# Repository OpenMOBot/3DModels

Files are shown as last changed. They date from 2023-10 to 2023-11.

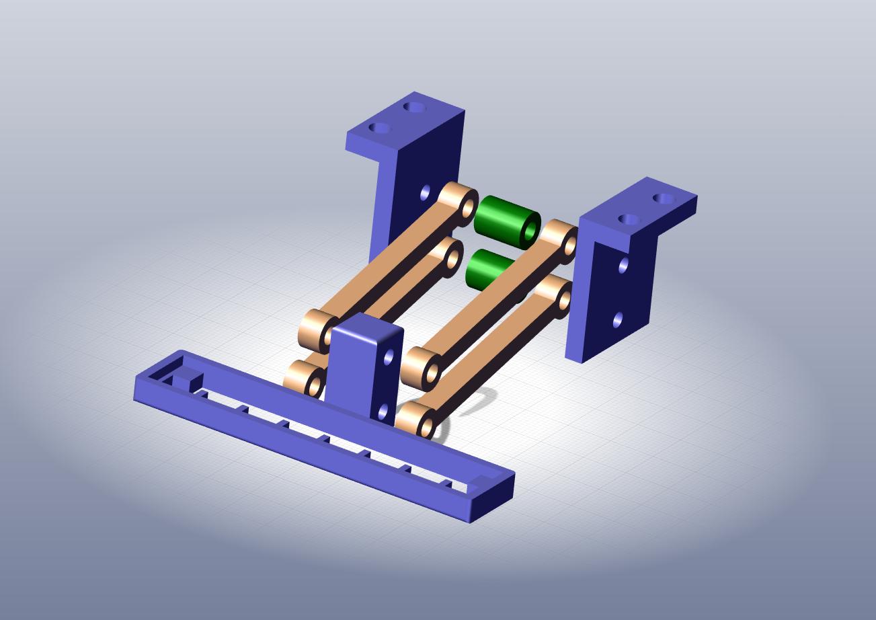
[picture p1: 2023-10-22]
images/sensor_holder_parts_assembly.jpg

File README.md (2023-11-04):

#  <span style="color: #32FAE5"> 1. How to assemble the 3D printed chassis :rocket:</span> 

## <span style="color: #32FAE5">1.1 Needed parts to be printed</span> 

- 1 :heavy_multiplication_x: [chassis](https://github.com/OpenMOBot/3DModels/blob/17b4ab84576b85b1f8e65cfbf05c9b37ba42eddf/design_stl/chassis/chassis.STL) <br />
- 4 :heavy_multiplication_x: [motor mount](https://github.com/OpenMOBot/3DModels/blob/17b4ab84576b85b1f8e65cfbf05c9b37ba42eddf/design_stl/chassis/motor_mount.STL) <br />
- 2 :heavy_multiplication_x: [encoder wheel](https://github.com/OpenMOBot/3DModels/blob/17b4ab84576b85b1f8e65cfbf05c9b37ba42eddf/design_stl/encoder_wheels/encoder_wheel_v4_20.STL) <br />
- 2 :heavy_multiplication_x: [mounting part](https://github.com/OpenMOBot/3DModels/blob/17b4ab84576b85b1f8e65cfbf05c9b37ba42eddf/design_stl/sensor_holder/mounting_part.STL) <br />
- 1 :heavy_multiplication_x: [sensor holder](https://github.com/OpenMOBot/3DModels/blob/17b4ab84576b85b1f8e65cfbf05c9b37ba42eddf/design_stl/sensor_holder/sensor_holder.STL) <br /> 
- 2 :heavy_multiplication_x: [spacer](https://github.com/OpenMOBot/3DModels/blob/17b4ab84576b85b1f8e65cfbf05c9b37ba42eddf/design_stl/sensor_holder/spacer.STL) <br />
- 4 :heavy_multiplication_x: [sturt](https://github.com/OpenMOBot/3DModels/blob/17b4ab84576b85b1f8e65cfbf05c9b37ba42eddf/design_stl/sensor_holder/sturt.STL) <br />
- 1  :heavy_multiplication_x:  [ultrasonic_holder](https://github.com/OpenMOBot/3DModels/blob/main/design_stl/chassis/ultrasonic-holder.stl)

## <span style="color: #32FAE5">1.2 Assemble the QTR-8RC sensor holder</span>

- Needed parts
sensor_holder_parts

- Assemble the mentioned parts
sensor_holder_parts_assembly

- Secure the sensor holder by using M3x30 and M3x25 bolts along with M3 nuts.
<p align="center">
    
</p>

## <span style="color: #32FAE5">1.3 Mount the caster wheel to the chassis</span>
- use four M4x8 bolts along with four M4 nuts and washers.
<p align="center">
    
</p>

## <span style="color: #32FAE5">1.4 Mount the Arduino and the DC motor driver L298N</span>

### Materials:
- Arduino coupling nuts: M3X30
- Motor driver coupling nuts: M3X12
- Bolts: M3x8 (for coupling nuts)
- Bolts: M3x5 (for securing components)
- Metal washers

### Install Coupling Nuts:

1. Attach M3x8 bolts through the chassis, securing coupling nuts.
2. Use washers and coupling nuts to fasten them tightly.

### Mount DC Motor Driver (L298N):

1. Place metal washers for stability.
2. Position the motor driver on the coupling nuts.
3. Use M3x5 bolts to the Motor Driver.

### Attach Arduino:

1. Set the Arduino board on the same coupling nuts.
2. Use M3x5 bolts to secure the arduino.
<p align="center">
    
</p>

## <span style="color: #32FAE5">1.5 Mount the 2 battery holders to the chassis</span>

- Attach the battery holders to the chassis using M3x8 bolts, securing them in place with M3 nuts and washers.
<p align="center">
    
</p>

## <span style="color: #32FAE5">1.6 Mount mottors and wheels to the chassis</span>

- Insert the planks designed to accommodate the DC motors into their respective slots, ensuring they are oriented to face the bottom of the robot and mount the motors and screw them with M3x30 bolts along with M3 nuts and washers.

<p align="center">
    
</p>

## <span style="color: #32FAE5">1.7 Mount the encoders(LM393) to the chassis</span>

- Secure the encoders using M3x14 bolts and M3 nuts and washers.

<p align="center">
    
</p>

## <span style="color: #32FAE5">1.8 Mount the servo motor</span>

- Secure the servo motor using M2x10 bolts and M2 nuts and washers.

<p align="center">
    
</p>

## <span style="color: #32FAE5">1.9 Mount QTR sensor holder that was assembled earlier [1.2]</span>

- Secure the sensor holder using M4x12 bolts and M4 nuts and washers.

<p align="center">
    
</p>

## <span style="color: #32FAE5">1.10 Mount the ultrasonic sensor and the QTR sensor to the holders</span>
- Secure the ultrasonic sensor holder using the screws in the servo motor package.

<p align="center">
    
</p>

# <span style="color: #32FAE5">2. Final 360 view </span>

<p align="center">
    
</p>

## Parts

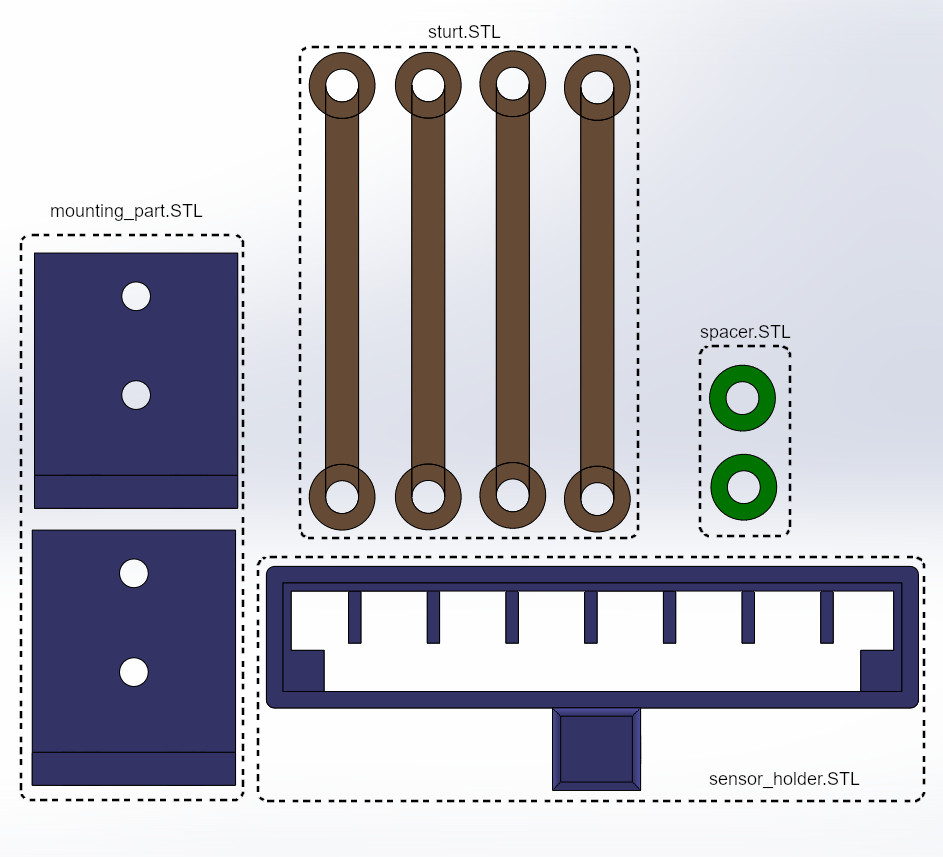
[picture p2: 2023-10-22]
images/sensor_holder_parts.png

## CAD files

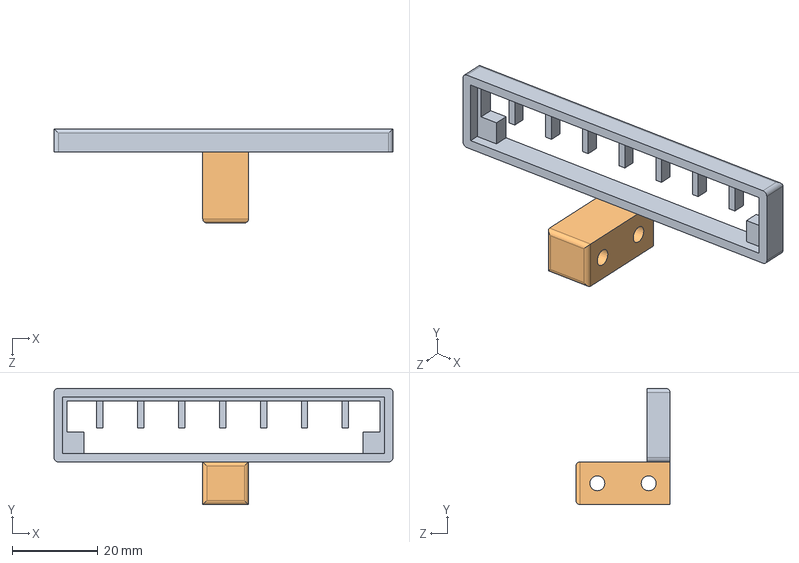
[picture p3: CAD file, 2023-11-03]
design_sldptr/sensor_holder/sensor_holderv2.SLDASM
79.2 x 27.2 x 22.0 mm
sensoren_durjach
prikachvach

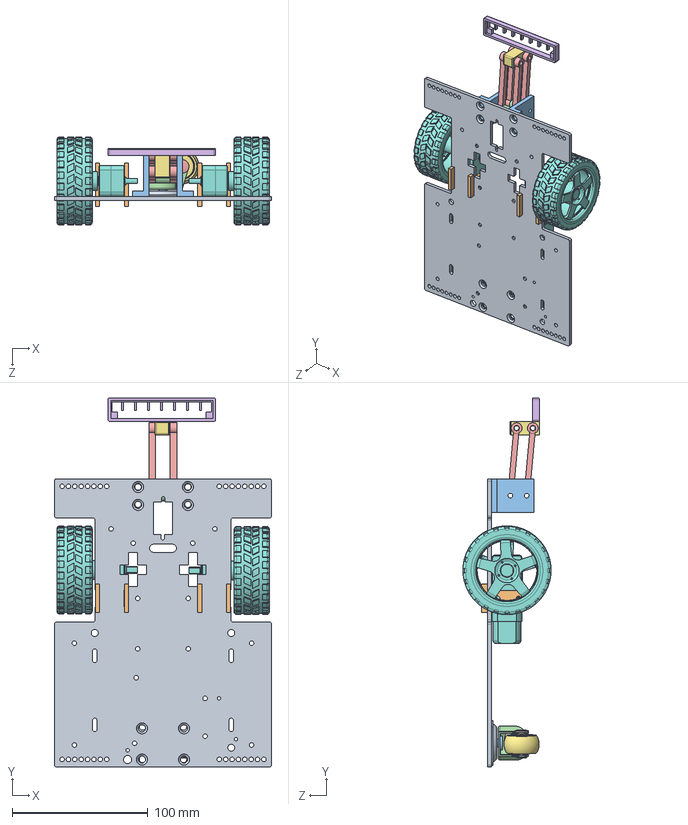
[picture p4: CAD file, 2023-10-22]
design_sldptr/chassis/Chassis_assembly.SLDASM
160.0 x 272.0 x 65.0 mm
chassis
motor_mount x 4
mounting_part x 2
spacer x 2
sturt_rod x 4
sensoren_durjach
prikachvach
dc_motor_with_wheel x 2
Base CW01
Rivet A CW01
Rivet B CW01
Chape CW01
Rivet2 A CW01
Rivet2 B CW01
Roue Libre CW01 - Galet

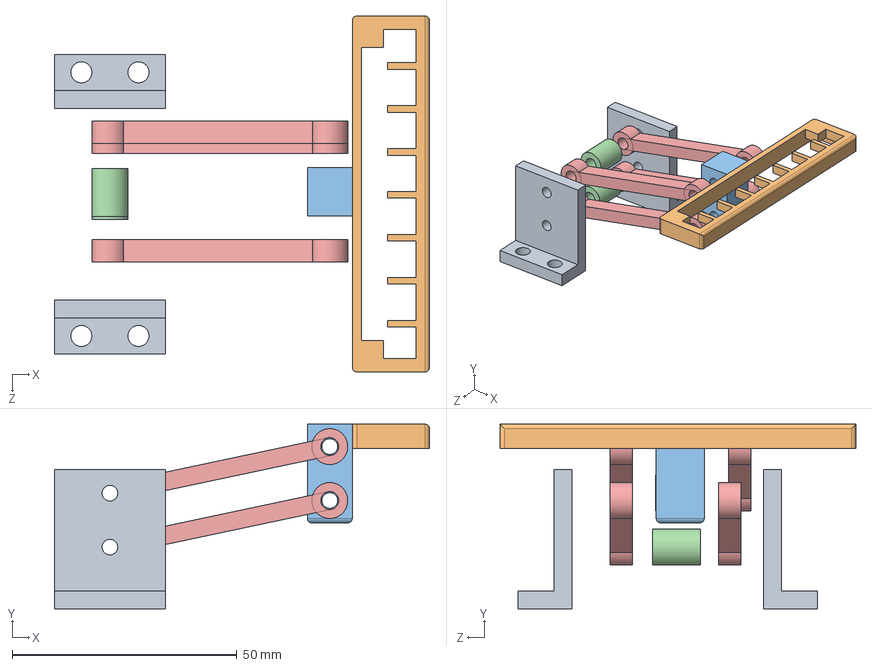
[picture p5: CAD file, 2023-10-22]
design_sldptr/sensor_holder/sensor_holder_parts_assembly.SLDASM
83.5 x 41.1 x 79.2 mm
mounting_part x 2
sensoren_durjach
prikachvach
spacer x 2
sturt_rod x 4

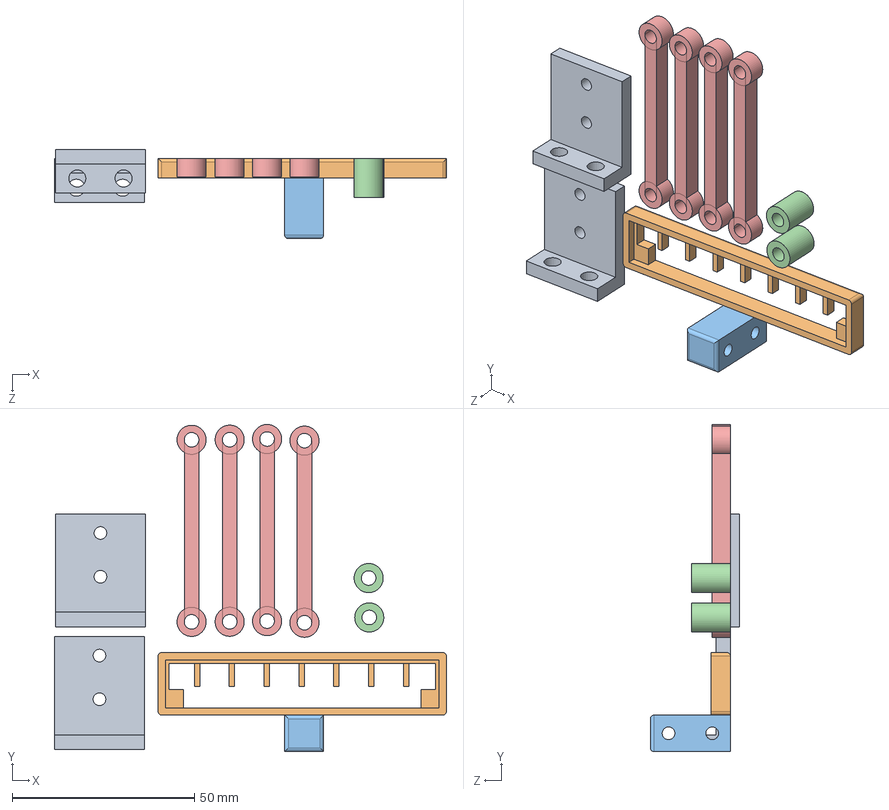
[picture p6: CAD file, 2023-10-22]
design_sldptr/sensor_holder/sensor_holder_parts.SLDASM
107.6 x 89.8 x 24.5 mm
mounting_part x 2
sensoren_durjach
prikachvach
spacer x 2
sturt_rod x 4

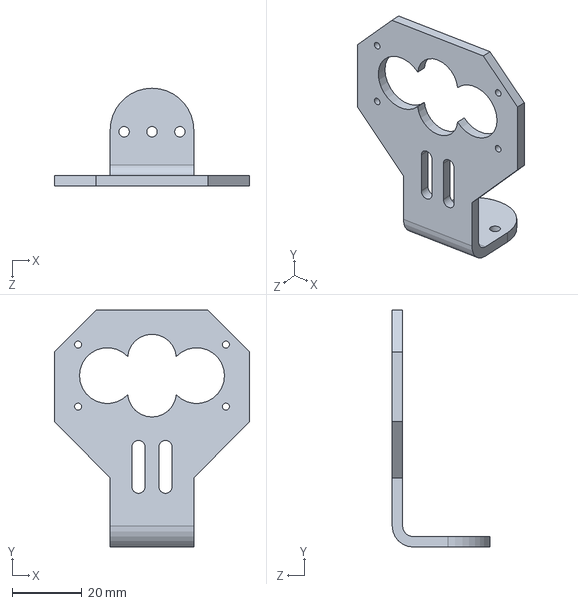
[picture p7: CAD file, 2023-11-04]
design_sldptr/chassis/utrasonic_holder.SLDPRT
56.0 x 68.0 x 28.0 mm

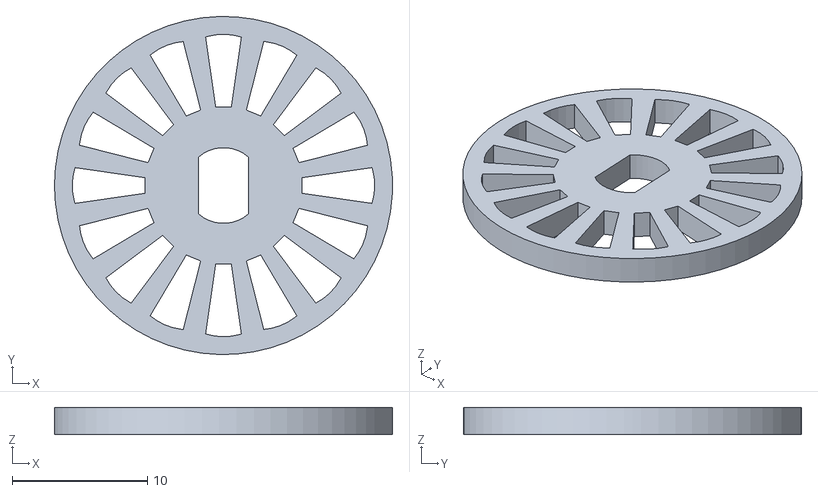
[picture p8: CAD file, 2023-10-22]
design_stl/encoder_wheel_v2.STL
25.0 x 25.0 x 2.00

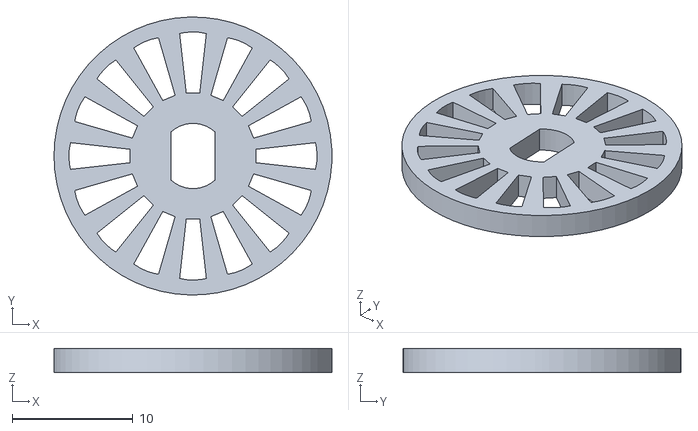
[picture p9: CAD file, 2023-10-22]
design_stl/encoder_wheels/encoder_wheel.STL
23.0 x 23.0 x 2.00

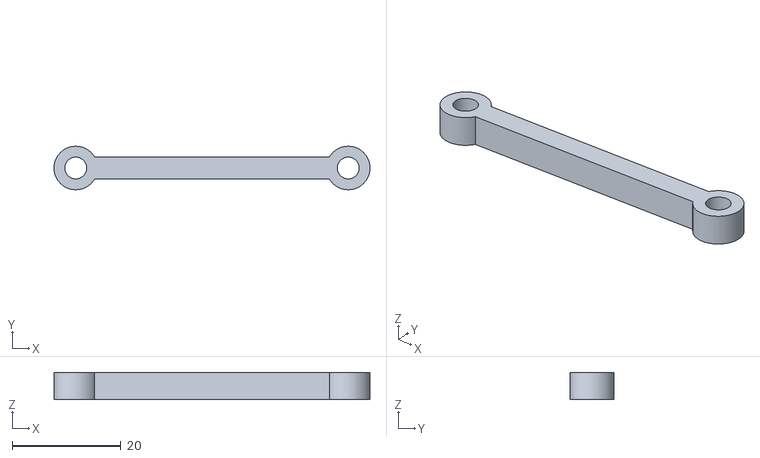
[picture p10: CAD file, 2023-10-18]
design_stl/sensor_holder/sturt.STL
58.0 x 8.00 x 5.00

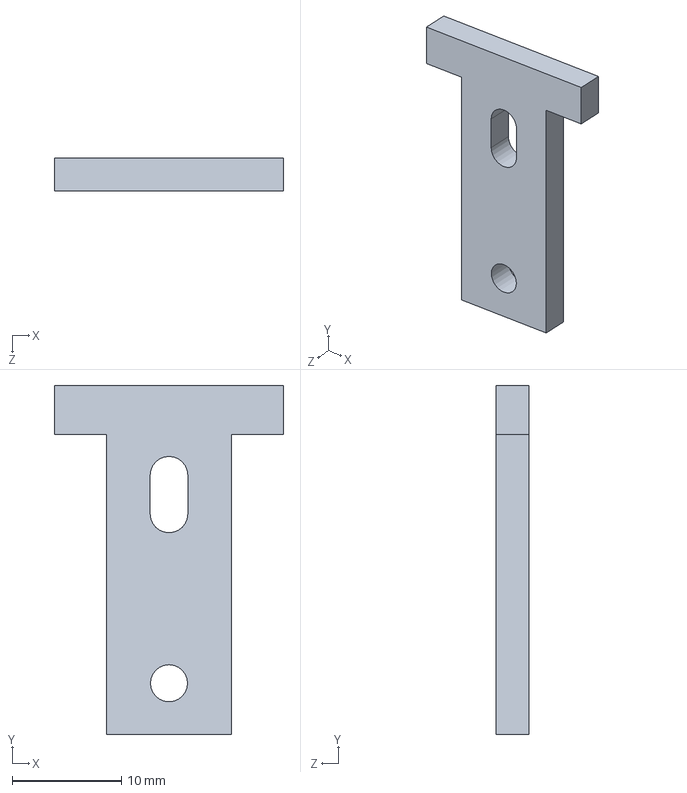
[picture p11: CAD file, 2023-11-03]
design_sldptr/chassis/motor_mount.SLDPRT
21.0 x 32.0 x 3.00 mm

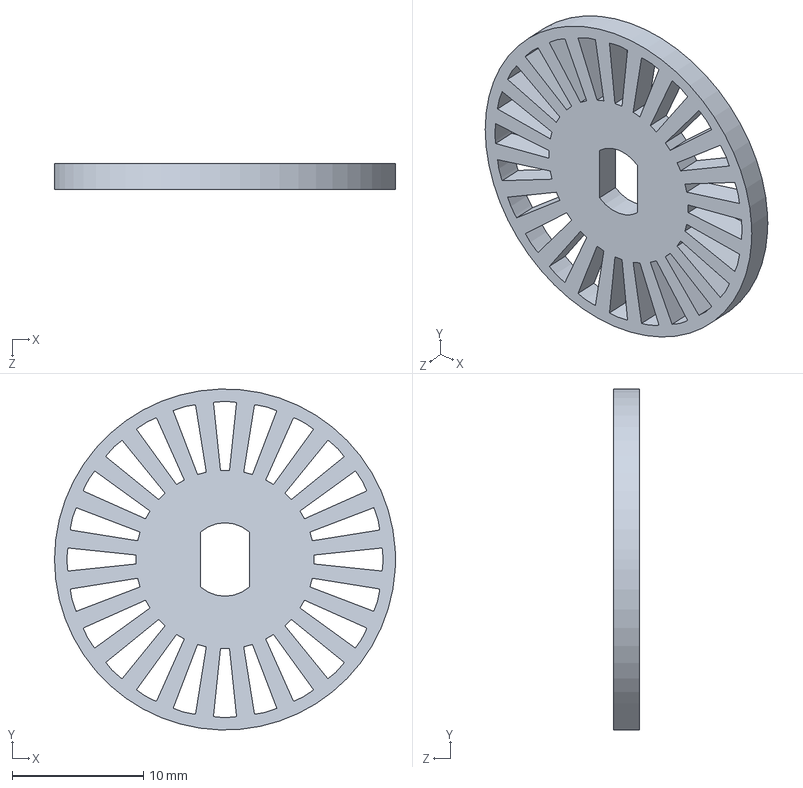
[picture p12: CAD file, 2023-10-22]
design_sldptr/encoder_wheels/encoder_wheel_v4_24.SLDPRT
26.0 x 26.0 x 2.00 mm

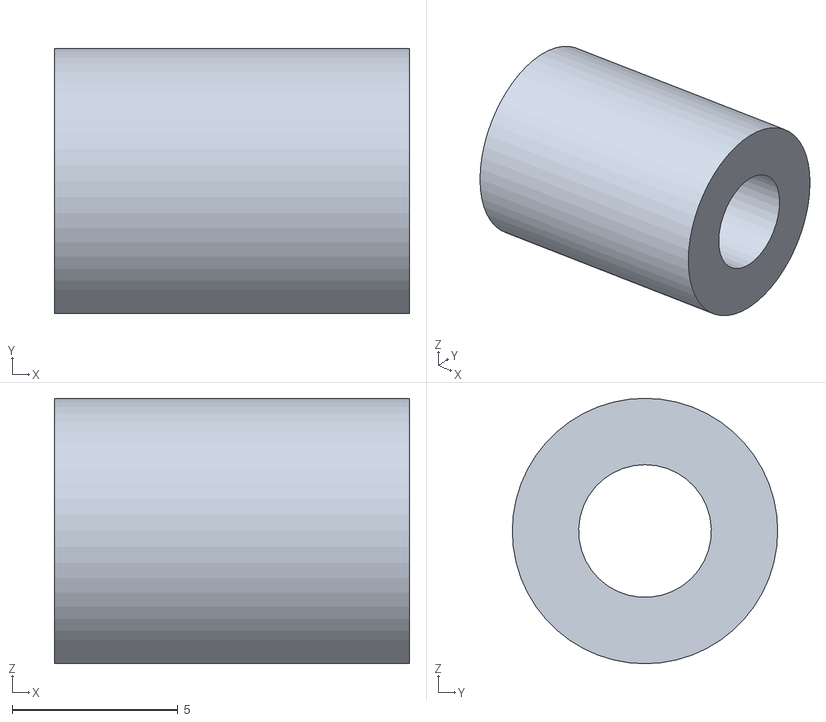
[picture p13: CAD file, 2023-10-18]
design_stl/sensor_holder/spacer.STL
10.7 x 8.00 x 8.00

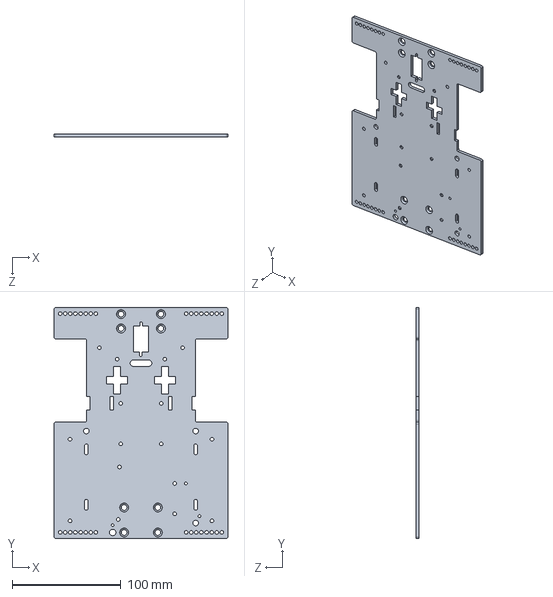
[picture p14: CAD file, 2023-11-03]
design_sldptr/chassis/chassis.SLDPRT
160.0 x 212.5 x 3.00 mm

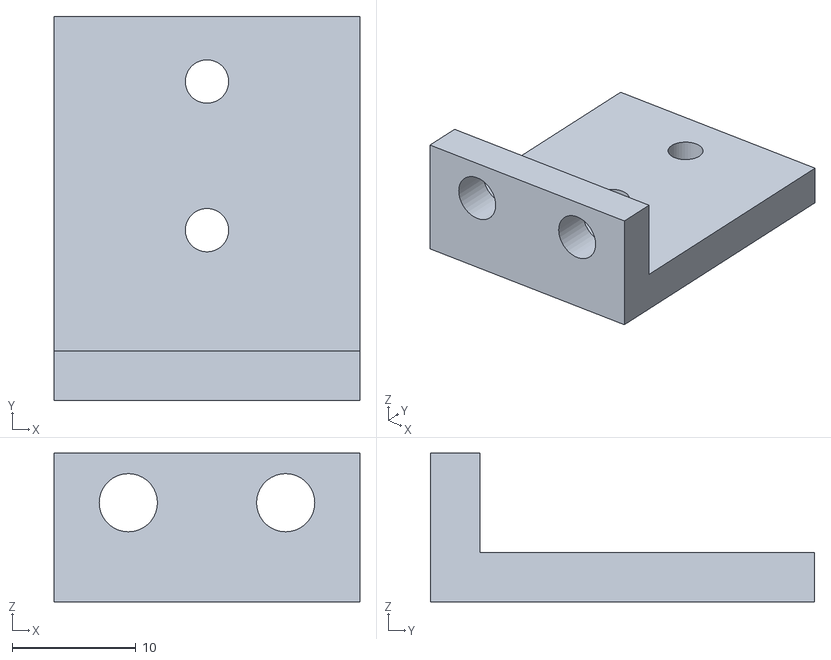
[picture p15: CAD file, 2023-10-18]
design_stl/sensor_holder/mounting_part.STL
24.7 x 31.0 x 12.0

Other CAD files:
design_stl/chassis/ultrasonic-holder.stl
design_stl/chassis/motor_mount.STL
design_sldptr/sensor_holder/spacer.SLDPRT
design_stl/chassis/chassis.STL
design_stl/encoder_wheels/encoder_wheel_v4_24.STL
design_sldptr/encoder_wheels/encoder_wheel.SLDPRT
design_sldptr/encoder_wheels/encoder_wheel_v2.SLDPRT
design_sldptr/encoder_wheels/encoder_wheel_v3.SLDPRT
design_sldptr/encoder_wheels/encoder_wheel_v4_20.SLDPRT
design_sldptr/sensor_holder/mounting_part.SLDPRT
design_sldptr/sensor_holder/sensor_holder_parts_assembly_bolts_nut2s.SLDASM
design_sldptr/sensor_holder/sensor_holder_parts_assembly_bolts_nuts.SLDASM
design_sldptr/sensor_holder/sturt_rod.SLDPRT
design_stl/encoder_wheels/encoder_wheel_v2.STL
design_stl/encoder_wheels/encoder_wheel_v3.STL
design_stl/encoder_wheels/encoder_wheel_v4_20.STL
design_stl/sensor_holder/sensor_holder.STL

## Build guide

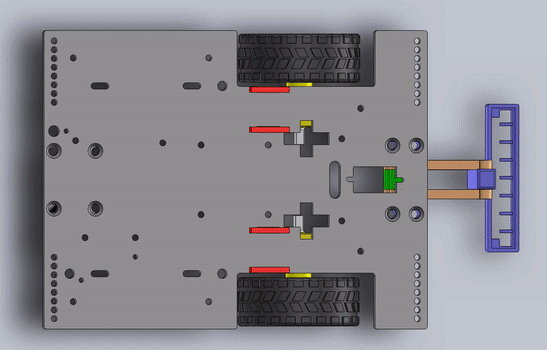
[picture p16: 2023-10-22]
images/assembly.gif

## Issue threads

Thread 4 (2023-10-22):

Doc

orlin369, 2023-10-22:
1 ✖️ 3DModels/design_stl/chassis/chassis.STL
4 ✖️ 3DModels/design_stl/chassis/motor_mount.STL
2 ✖️ 3DModels/design_stl/encoder_wheels/encoder_wheel_v4_20.STL
2 ✖️ 3DModels/design_stl/sensor_holder/mounting_part.STL
1 ✖️ 3DModels/design_stl/sensor_holder/sensor_holder.STL
2 ✖️ 3DModels/design_stl/sensor_holder/spacer.STL
4 ✖️ 3DModels/design_stl/sensor_holder/sturt.STL

To be as links to the target file.

majvazov, 2023-10-23:
Done

Closed 2023-10-23.

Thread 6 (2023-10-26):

Finish the: 3. Mount the motors to the chassis

orlin369, 2023-10-26:
Please finish this built by adding render pictures of the model and little bit of text to describe the process.

[3. Mount the motors to the chassis](https://github.com/OpenMOBot/3DModels#3-mount-the-mottors-to-the-chassis)

Closed 2023-11-06.

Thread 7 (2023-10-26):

Finis the: 1. How to assemble the 3D printed chassis 🚀

orlin369, 2023-10-26:
Please add process description of the printing the parts and some printer settings, because this can cost issues when some one try to print the parts.
Please add some hints and good printing practices for this particular parts of the robot.

Example: nuzzle diameter, material, filling of the part, speed of printing, bed temperature and so on....

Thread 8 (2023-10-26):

Bullit 5

orlin369, 2023-10-26:
Please add bullet 5 and there add 3D model of the Arduino, distance nuts, batteries, power switch and so on.

The parts for printing and 3D model can stay separated in two parts STL for printing and full model for development.

Please create a separate directory with exports in STL format of all part I mean ALL.
This directory will be used for creating a animated 3D robot model for virtual usage in separate repository, but this one will be source of the 3D models.
This virtual robot model will be use in later workshops for writing a software and algorithm without having an actual robot.
OR creating a Digital TWIN.

We can talk about later purpose of the models in our working group chat.

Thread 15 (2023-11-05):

Front wheel issue

VASILEVGEORGE, 2023-11-05:
Front wheel push both battery packs.
Possible solutions
1. Move battery packs down
2. Make board larger

VASILEVGEORGE, 2023-11-05:
![Uploading IMG_20231105_105429.jpg…]()

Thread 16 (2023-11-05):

The positions washers is not correct on section 1.6

barzakov, 2023-11-05:
In section:
1.6 Mount mottors and wheels to the chassis
The positions washers is not correct.
Please review the animation.

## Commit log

2023-10-18 First version line follower chassis
    [chassis.SLDPRT, chassis.STL, motor_mount.SLDPRT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]
2023-10-18 Adding fillets to the sensor_holder
    [sensor_holder.SLDPRT, sensor_holder.STL, sensor_holderv2.SLDASM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]
2023-10-22 Adding some encoder plates, readme and assembly design
    [Chassis_assembly.SLDASM, chassis.SLDPRT, encoder_wheel.SLDPRT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]
2023-10-22 removing cached files
    [Chassis_assembly.SLDASM, chassis.SLDPRT, motor_mount.SLDPRT]
2023-10-22 removing encoder plate cached file
2023-10-22 Adding gif of the assembled chassis
2023-10-22 Adding instructions how to assemble the robot
    [chassis.SLDPRT, sensor_holder_parts.SLDASM, sensor_holder_parts_assembly.SLDASM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]
2023-11-03 Adding final readme details and finalized sadlsms
    [chassis.SLDPRT, encoder_wheel_v4_20.SLDPRT, motor_mount.SLDPRT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]
2023-11-04 Adding ultrasonic sensor holder
    [ultrasonic-holder.stl, utrasonic_holder.SLDPRT]
2023-11-04 Adding ultrasonic holder to the readme file
